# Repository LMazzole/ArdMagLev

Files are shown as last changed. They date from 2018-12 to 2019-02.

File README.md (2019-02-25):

# ArdMagLev
This Project is based on the [AirBonsai](https://www.instructables.com/id/Arduino-Air-Bonsai-Levitation/)-Project from Funelab.  

- [General Setup](#general-setup)
- [Initial Problems](#initial-problems)
- [Improvments](#improvments)
- [Result](#result)
- [Remaining Problems](#remaining-problems)
- [TODO's](#todos)

## General Setup
### IDE
[PlatformIO ](https://platformio.org/platformio-ide)

### Board
Arduino Leonardo

## Initial Problems

### Coils
One of the biggest Problems is, that the generated Field of the Coils will disturb your Hallsensor.  
Without the correct Sensorvalue you won't be able to controll the position.
[TODO: Add Calculation Tau]
### Position of the Hallsensor
The proposed setup with the Breadboard has the disadvantage, that you're not able to orient the Hallsensor correctly. Horizontal und vertical displacements have a negative influence on the precision of the Sensors and increase the disturbance from the Coils.  

As you can see in the Image below the Sensor will detect the Field from the Coils much more if they are not completly parallel.  

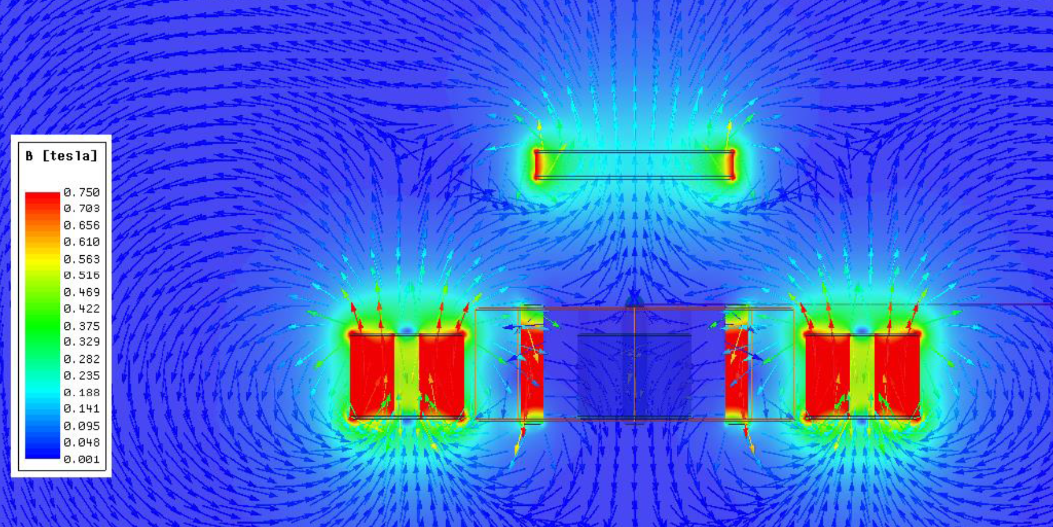
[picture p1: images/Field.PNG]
Field


## Improvements

### System-Overview

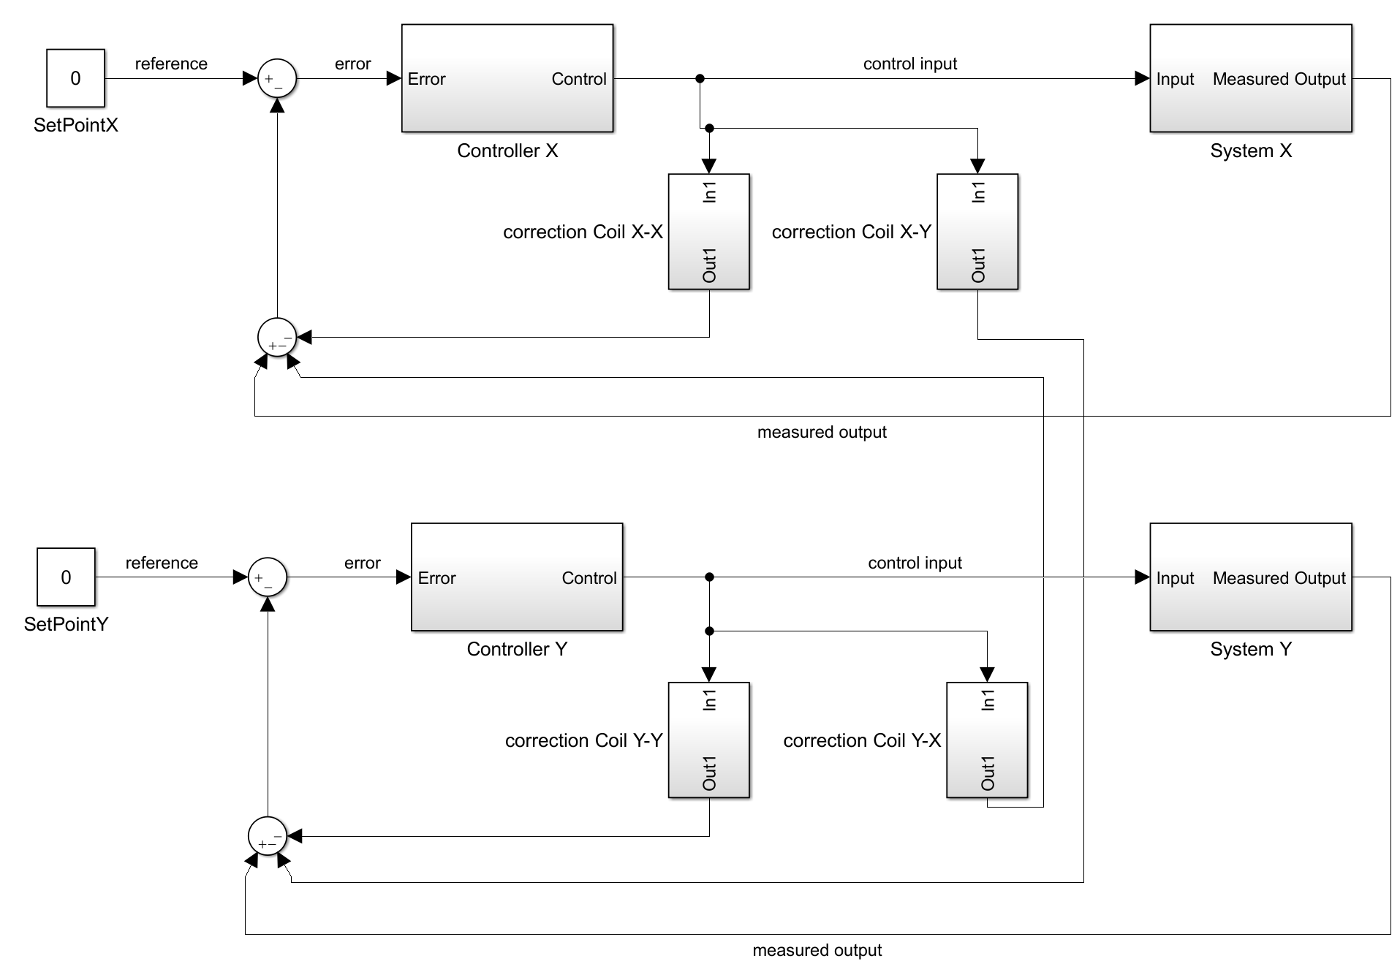
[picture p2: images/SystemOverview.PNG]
SystemOverview


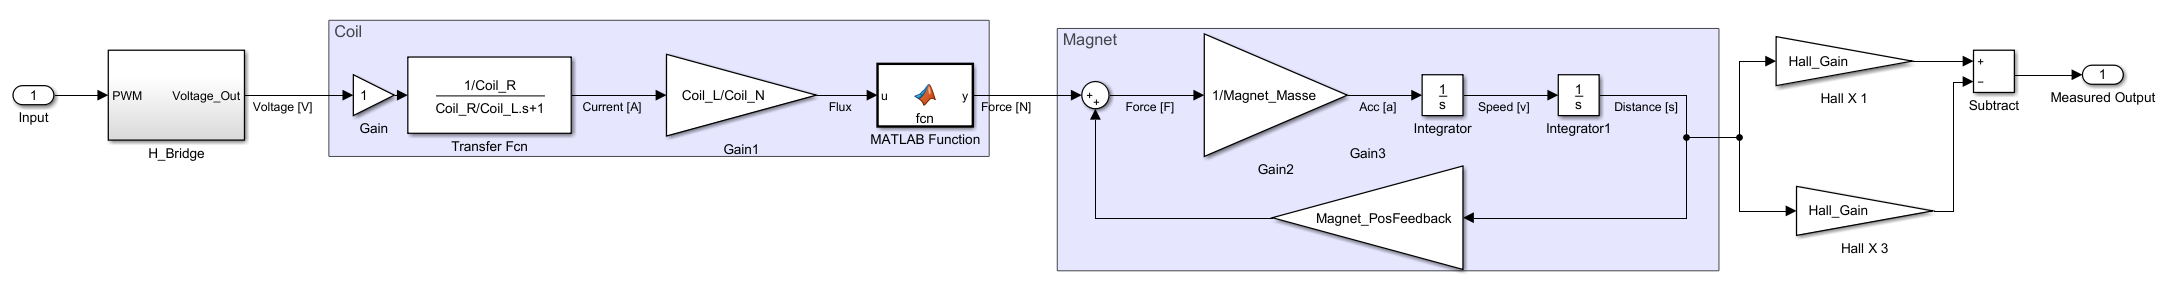
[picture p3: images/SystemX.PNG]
SystemX


### Hardware
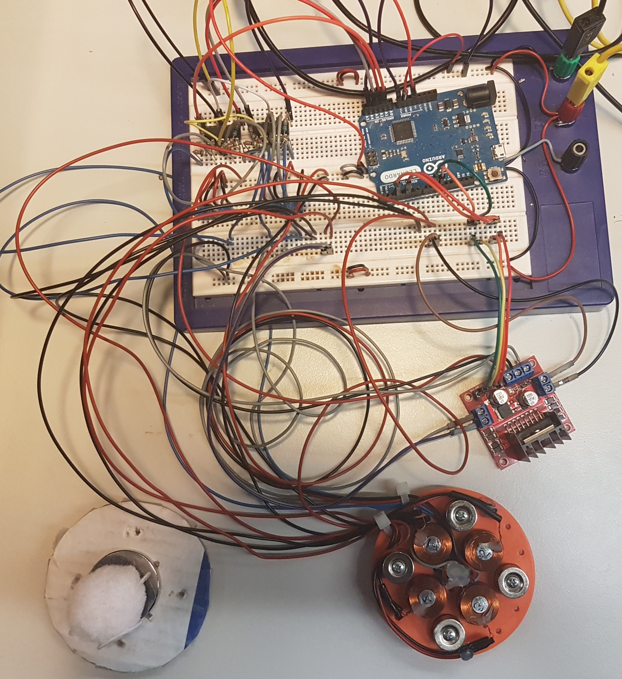
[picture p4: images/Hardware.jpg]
Hardware


### 3D-Print
To solve the Position-Problem and make a more reproducible Design a 3D-Print was created. 

[Check the Folder](./3D-Data/) for the .stl or .prt (Siemens NX 12)

### Hall-Sensors
[SS495A-S Datasheet](https://sensing.honeywell.com/honeywell-sensing-sensors-linear-hall-effect-ics-ss490-series-datasheet-005843-2-en.pdf)  
To minimize the Coil-influence, two more Hallsensores were added.  

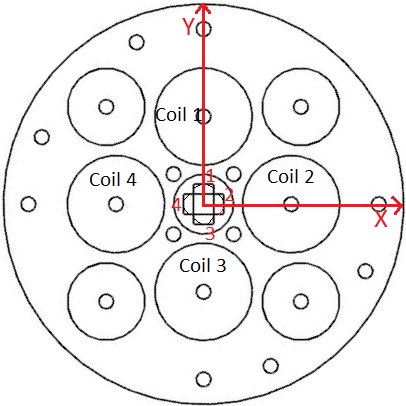
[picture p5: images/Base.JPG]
Base


### Software
#### Preprocessor Directives
To switch between the different Modes comment or uncomment the #defines at the beginning of the Sketch.

##### MYDEBUG
This Mode will display debugg-messages over the Serial-Port

##### MYTIMING
This Mode will display the time needed for one Loop  over the Serial-Port

##### TESTX
This Mode will power the Coils on the X-Axis in Steps from 0 to 255 and 0 to -255.  

At 255 your Input_X should be an negativ Value.  
At -255 your Input_X should be an positiv Value.
##### TESTY
This Mode will power the Coils on the Y-Axis in Steps from 0 to 255 and 0 to -255.  

At 255 your Input_Y should be an negativ Value.  
At -255 your Input_Y should be an positiv Value.
##### TESTXY
This Mode will move your Magnet in an rectangle.

##### CONTROLL
This Mode will activate the PID-Controller.

##### AUTOSHUTDOWN
This Mode will activate the Autoshutdown.  
If your Controll fails and the Magnet falls from its centerpoint the Controller will set the PWM to 100%. This will overheat your Coils and destroy them.  

To prevent this, the Autoshutdown will power off the Coils if the Output is too high for too long.

##### BREAKMODE

An Instructabel User recommended to use the breaking mode for the H-Bridge.  

>After playing around with the H bridge I found that its output current is way more predictable by leaving the jumpers on ENA and ENB, and applying pwm directly to the IN pins: (eg: If the output value from the pid is positive, IN1 is low, and IN2 is fed the pwm wave. If the output is negative, IN2 is low, and IN1 is fed the pwm wave). This is the "braking mode" when the bridge is used to drive dc motors, so the coil ends are short circuited between the pwm pulses instead of being at high impedance.
> -- <cite> Simo_Dax </cite> 

#### Corrct Coil-Influence
The function *corr_sensor_x* and *corr_sensor_y* will read the actual PWM-Output and calculate the error generated in the Sensors. You probably will need to update this calculation for your own setup.

## Result
Base

### Technical Details
- Max Load: [Todo: measure]
- Normal Power-consumption: ca. 0.4 A
- Max Power-consumption: ca. 2.5 A

## Remaining Problems

### Tuning/Stability
A little bit of luck is needed to find the correct parameters. If your about 0.2 off it will probably not be stable.

### Noise
Unfortunately because of the low PWM frequency the Coils are VERY noisy.  
An Higher PWM frequency would solve this Problem.

### Magnet detection
There is no Standby-Mode atm. A Function for the detection of the floating Magnet is necessary.

## TODOs
Feel free to contribute
- Improve Instructions
- Update Controller for Higher PWM and to minimize Coil-Noise
- Implement detection for the floating magnet
- Write an PID-Controller and delete the library

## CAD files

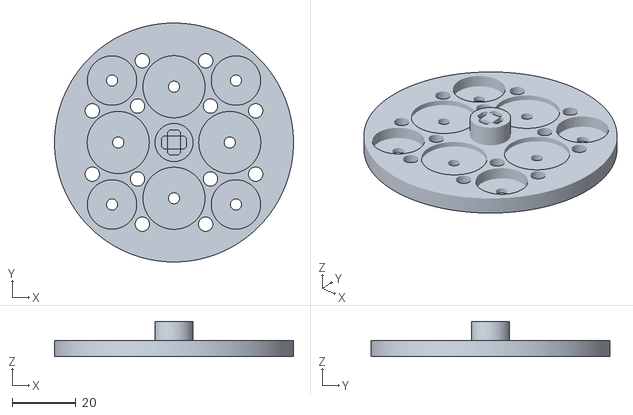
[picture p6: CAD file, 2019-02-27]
3D-Data/MagLev-Base_V3.stl
75.0 x 75.0 x 11.0

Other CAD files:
3D-Data/MagLev-Base_V3.prt

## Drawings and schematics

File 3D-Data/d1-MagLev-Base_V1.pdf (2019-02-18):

1

A

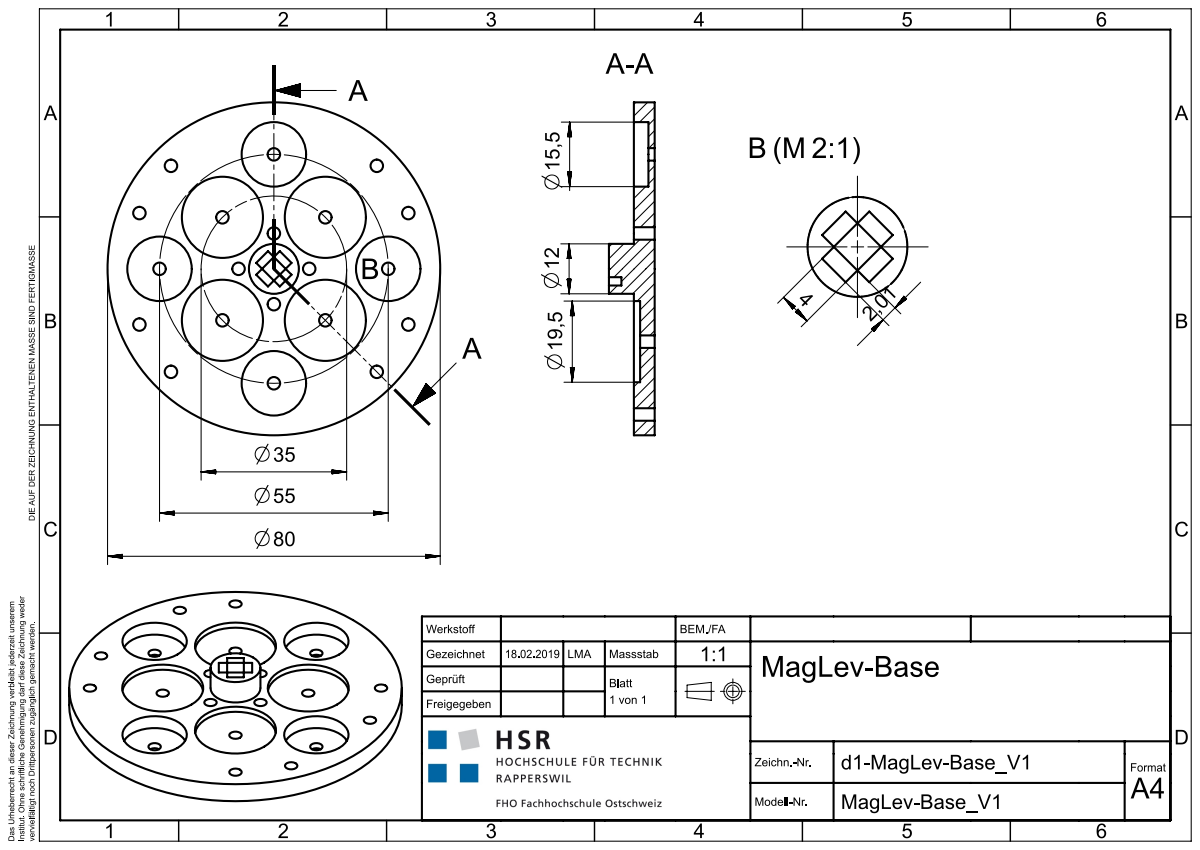
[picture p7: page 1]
Werkstoff; BEM./FA; Gezeichnet; LMA; Massstab; Geprüft; MagLev-Base Blatt; Freigegeben; 1 von 1; Zeichn.-Nr.; d1-MagLev-Base_V1; Format; Modell-Nr.; A4 MagLev-Base_V1

vervielfältigt noch Drittpersonen zugänglich gemacht werden. DIE AUF DER ZEICHNUNG ENTHALTENEN MASSE SIND FERTIGMASSE

Das Urheberrecht an dieser Zeichnung verbleibt jederzeit unserem

Institut. Ohne schriftliche Genehmigung darf diese Zeichnung weder

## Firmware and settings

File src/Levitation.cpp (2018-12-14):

#include <PID_v1.h>
#include "Arduino.h"

// #define MYDEBUG
// #define MYTIMING

#define CONTROLL
// #define TESTX
// #define TESTY
// #define TESTXY

//Define Debug-Function
#ifdef MYDEBUG
  #define DEBUG_PRINT(x)        Serial.print (x)
  #define DEBUG_PRINTDEC(x)     Serial.print (x, DEC)
  #define DEBUG_PRINTLN(x)      Serial.println (x)
#else
  #define DEBUG_PRINT(x)
  #define DEBUG_PRINTDEC(x)
  #define DEBUG_PRINTLN(x)
#endif

#ifdef MYTIMING
  #define TIMING_PRINT(x)        Serial.print (x)
  #define TIMING_PRINTDEC(x)     Serial.print (x, DEC)
  #define TIMING_PRINTLN(x)      Serial.println (x)
#else
  #define TIMING_PRINT(x)
  #define TIMING_PRINTDEC(x)
  #define TIMING_PRINTLN(x)
#endif

const byte ENA = 10;
const byte IN1 = 9; //9Enable for Out 1 X_Plus
const byte IN2 = 8; //8Enable for Out 2 X_Minus
const byte IN3 = 7; //Enable for Out 3 Y_Plus
const byte IN4 = 6; //Enable for Out 4 Y_Minus
const byte ENB = 5;
const byte HALLX = A1;
const byte HALLY = A0;

const byte anzahlMittelWerte = 3;
int werteHallX[anzahlMittelWerte], zaehlerMittelWerteX=0;
int werteHallY[anzahlMittelWerte], zaehlerMittelWerteY=0;
int mittelWertX(int neuerWert);
int mittelWertY(int neuerWert);

unsigned long time_loop_start;
unsigned long time_loop_stop;

double Setpoint_X, X_plus;
static double Input_X, Output_X;
double p_X = 2,i_X = 0,d_X = 0.005;
// double p_X = 1.0,i_X = 0.0,d_X = 0.01;

double Setpoint_Y, Y_plus;
static double Input_Y, Output_Y;
double p_Y = 2,i_Y = 0,d_Y = 0.005;
// double p_Y = 1.0,i_Y = 0.0,d_Y = 0.01;
PID PID_X(&Input_X, &Output_X, &Setpoint_X, p_X,i_X,d_X, DIRECT);
PID PID_Y(&Input_Y, &Output_Y, &Setpoint_Y, p_Y,i_Y,d_Y, DIRECT);

void turn_X(int a);
void turn_Y(int a);
void read_sensor();
void turn_off();
int corr_sensor_y(double pwm_y);
int corr_sensor_x(double pwm_x);
double pid_ctrl_X(double error);
double pid_ctrl_Y(double error);


void setup(){
  Serial.begin(4800);
  pinMode(IN1,OUTPUT);
  pinMode(IN2,OUTPUT);
  pinMode(IN3,OUTPUT);
  pinMode(IN4,OUTPUT);
  pinMode(ENA,OUTPUT);
  pinMode(ENB,OUTPUT);

  digitalWrite(IN1,0);
  digitalWrite(IN2,0);
  digitalWrite(IN3,0);
  digitalWrite(IN4,0);
  analogWrite(ENA,0);
  analogWrite(ENB,0);


  Setpoint_X = 560;//560;
  PID_X.SetTunings(p_X,i_X,d_X);
  PID_X.SetOutputLimits(-255,255);
  PID_X.SetSampleTime(10);//10
  PID_X.SetMode(AUTOMATIC);
  PID_X.SetControllerDirection(REVERSE);

  Setpoint_Y = 560;//560;
  PID_Y.SetTunings(p_Y,i_Y,d_Y);
  PID_Y.SetOutputLimits(-255,255);
  PID_Y.SetSampleTime(10);//10
  PID_Y.SetMode(AUTOMATIC);
  PID_Y.SetControllerDirection(REVERSE);//DIRECT or REVERSE

turn_off();
}

void loop(){
  // DEBUG_PRINTLN("");
  TIMING_PRINT("Time passed [ms]:"); TIMING_PRINTLN((double)(time_loop_stop-time_loop_start));
  time_loop_start=millis();
  Input_X = analogRead(HALLX)-corr_sensor_y(Output_X);
  Input_Y = analogRead(HALLY)-corr_sensor_y(Output_Y);
  // Input_X = mittelWertX(Input_X);
  // Input_Y = mittelWertY(Input_Y);
    // read_sensor();
  #ifdef CONTROLL //Regeln
  read_sensor();
    //Compute correction Value
    //===PID====
    // time_loop_stop=millis();
    // TIMING_PRINT("Time passed [ms]:"); TIMING_PRINTLN((double)(time_loop_stop-time_loop_start));
    PID_X.Compute();
    PID_Y.Compute();
    // time_loop_start=millis();
    turn_X(Output_X);
    turn_Y(Output_Y);
  #endif

  #ifdef TESTX
  DEBUG_PRINTLN("");
  DEBUG_PRINTLN("===TESTX====");
    int valx = 0;
    int delaytestx=750;
    while (valx<255) {
      turn_X(valx);
      read_sensor();
      valx+=10;
      delay(delaytestx);
    }
    turn_X(0);
    DEBUG_PRINTLN("=======");
    delay(1000);
    valx = 0;
    while (valx<255) {
      turn_X(-valx);
      read_sensor();
      valx+=10;
      delay(delaytestx);
    }
    turn_X(0);
    // delay(10000);
  #endif

  #ifdef TESTY
  DEBUG_PRINTLN("");
  DEBUG_PRINTLN("===TESTY====");
    int valy = 0;
    int delaytesty=750;
    while (valy<255) {
      turn_Y(valy);
      read_sensor();
      valy+=10;
      delay(delaytesty);
    }
    turn_Y(0);
    DEBUG_PRINTLN("=======");
    delay(1000);
    valy = 0;
    while (valy<255) {
      turn_Y(-valy);
      read_sensor();
      valy+=10;
      delay(delaytesty);
    }
    turn_Y(0);
    delay(5000);
  #endif

  #ifdef TESTXY
    DEBUG_PRINTLN("=====TESTXY=====");
    int delayTest=2000;
    turn_X(255); //Oben
    delay(delayTest);
    read_sensor();
    turn_off();
    turn_Y(255); //Rechts
    delay(delayTest);
    read_sensor();
    turn_off();
    turn_X(-255); //Unten
    delay(delayTest);
    read_sensor();
    turn_off();
    turn_Y(-255); //Links
    delay(delayTest);
    read_sensor();
    turn_off();
    read_sensor();
    delay(5000);
  #endif

  time_loop_stop=millis();
}

void turn_X(int a){
  Output_X=a;
  DEBUG_PRINT("turn_X: ");DEBUG_PRINT("\t"); DEBUG_PRINT(a);DEBUG_PRINT("\t");
  if(a>=0)  {
    DEBUG_PRINT(" Oben");
    digitalWrite(IN2,0);
    digitalWrite(IN1,1);
    analogWrite(ENA,a);
  }
  else  {
    DEBUG_PRINT(" Unten");
    a=-a;
    digitalWrite(IN1,0);
    digitalWrite(IN2,1);
    analogWrite(ENA,a);
  }
  // DEBUG_PRINT("\t");
  // DEBUG_PRINTLN("");
}

void turn_Y(int a){
  Output_Y=a;
DEBUG_PRINT("turn_Y: ");DEBUG_PRINT("\t"); DEBUG_PRINT(a);DEBUG_PRINT("\t");
  if(a>=0)  {
    DEBUG_PRINT(" Rechts");
    digitalWrite(IN4,0);
    digitalWrite(IN3,1);
    analogWrite(ENB,a);
  }
  else{
    DEBUG_PRINT(" Links");
    a=-a;
    digitalWrite(IN3,0);
    digitalWrite(IN4,1);
    analogWrite(ENB,a);
  }
  // DEBUG_PRINT("\t");
  // DEBUG_PRINTLN("");
}

void turn_off(){
  digitalWrite(IN1,0);
  digitalWrite(IN2,0);
  digitalWrite(IN3,0);
  digitalWrite(IN4,0);
  Output_X=0;
  Output_Y=0;
  analogWrite(ENA,Output_X);
  analogWrite(ENB,Output_Y);
  delay(100);
}

void read_sensor(){
  Input_X = analogRead(A1);
  Input_Y = analogRead(A0);
  DEBUG_PRINT("\t");
  // DEBUG_PRINT("\t");DEBUG_PRINT("\t");DEBUG_PRINT("\t");
  DEBUG_PRINT("Input_X: ");DEBUG_PRINT("\t");
  DEBUG_PRINT(Input_X);DEBUG_PRINT("\t");
  DEBUG_PRINT("corr: ");DEBUG_PRINT("\t");
  DEBUG_PRINT(Input_X-corr_sensor_x(Output_X));
  // DEBUG_PRINTLN("");//DEBUG_PRINT("\t");
  DEBUG_PRINT("\t");
  DEBUG_PRINT("Input_Y: ");DEBUG_PRINT("\t");
  DEBUG_PRINT(Input_Y);DEBUG_PRINT("\t");
  DEBUG_PRINT("corr: ");DEBUG_PRINT("\t");
  DEBUG_PRINT(Input_Y-corr_sensor_y(Output_Y));DEBUG_PRINTLN("");
}

int mittelWertX(int neuerWert) {
// neuen int Wert eingeben und den Mittelwert als fSloat zurück geben
//
// Matthias Busse 9.2.2016 Version 1.0
float mittel, summe=0;
  werteHallX[zaehlerMittelWerteX] = neuerWert;
  for(int k=0; k < anzahlMittelWerte; k++) summe += werteHallX[k];
  mittel=(float) summe / anzahlMittelWerte;
  zaehlerMittelWerteX++;
  if(zaehlerMittelWerteX >= anzahlMittelWerte) zaehlerMittelWerteX=0;
  return mittel;
}

int mittelWertY(int neuerWert) {
// neuen int Wert eingeben und den Mittelwert als float zurück geben
//
// Matthias Busse 9.2.2016 Version 1.0
float mittel, summe=0;
  werteHallY[zaehlerMittelWerteY] = neuerWert;
  for(int k=0; k < anzahlMittelWerte; k++) summe += werteHallY[k];
  mittel=(float) summe / anzahlMittelWerte;
  zaehlerMittelWerteY++;
  if(zaehlerMittelWerteY >= anzahlMittelWerte) zaehlerMittelWerteY=0;
  return mittel;
}

int corr_sensor_y(double x){
  // return 0;
  if (x==0){
    return 0;
  }
  else{
    double corrval;
    // corrval= 0.01*x*x*x - 0.88*x*x + 22*x;// -176;
    corrval=1.13/100000*x*x*x+9.70/1000000*x*x-0.08*x+0.113;
    // corrval= (0.1132*x - 0.0828)*x*x;
    // corrval=(0.000009*x*x-0.0001*x-0.08)*x; //corrval=(0.000009*x*x-0.0001*x-0.08)*x;
    // DEBUG_PRINTLN(corrval);
    // DEBUG_PRINTLN((int)corrval);
    return (int)corrval;
  }
}

int corr_sensor_x(double x){
  if (x==0){
    return 0;
  }
  else{
    double corrval;
    corrval=1.13/100000*x*x*x+9.70/1000000*x*x-0.08*x+0.113;
    // corrval=(0.000008*x*x-0.0001*x+0.006)*x;
    // DEBUG_PRINTLN(corrval);
    // DEBUG_PRINTLN((int)corrval);
    return (int)corrval;
  }
}
// double pid_ctrl_X(double error) { //PID without library
//   static double X_esum;
//   static double X_ealt;
//   double y;
//
//   esum = X_esum + error;
//   y = p_X * error + i_X * x_Ta * esum + d_X * (error – X_ealt)/X_Ta;
//   ealt = error;
//
//   return y;
// }

// double pid_ctrl_Y(double e) { //PID without library
//   static double esum;
//   static double ealt;
//   double y;
//
//   esum = esum + e;
//   y = Kp * e + Ki * Ta * esum + Kd * (e – ealt)/Ta;
//   ealt = e;
//
//   return y;
// }

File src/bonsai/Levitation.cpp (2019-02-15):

/*%
-----------------------------------------------------------------------
% Dateiname: Levitation.cpp

% Funktion: Regelung eines fliegenden Magneten
%           Grundlage: https://www.instructables.com/id/Arduino-Air-Bonsai-Levitation/
% Autor: Luca Mazzoleni  lmazzole@hsr.ch
%
% Erstellungsdatum: 08.12.2018
% Letzte Änderung:  19.12.2018
%-----------------------------------------------------------------------
*/


#include <PID_v1.h>
#include "Arduino.h"

// #define MYDEBUG
// #define MYTIMING

// #define TESTX
// #define TESTY
// #define TESTXY

#define CONTROLL
#define AUTOSHUTDOWN
#define BREAKERMODE


//Define Debug-Function
#ifdef MYDEBUG
  #define DEBUG_PRINT(x)        Serial.print (x)
  #define DEBUG_PRINTDEC(x)     Serial.print (x, DEC)
  #define DEBUG_PRINTLN(x)      Serial.println (x)
#else
  #define DEBUG_PRINT(x)
  #define DEBUG_PRINTDEC(x)
  #define DEBUG_PRINTLN(x)
#endif

#ifdef MYTIMING
  #define TIMING_PRINT(x)        Serial.print (x)
  #define TIMING_PRINTDEC(x)     Serial.print (x, DEC)
  #define TIMING_PRINTLN(x)      Serial.println (x)
  unsigned long time_loop_start;
  unsigned long time_loop_stop;
#else
  #define TIMING_PRINT(x)
  #define TIMING_PRINTDEC(x)
  #define TIMING_PRINTLN(x)
#endif

// PINMAPPING
#ifdef BUILD_FOR_NANO
  const byte ENA = 10;
  const byte IN1 = 9; //9Enable for Out 1 X_Plus
  const byte IN2 = 8; //8Enable for Out 2 X_Minus
  const byte IN3 = 7; //Enable for Out 3 Y_Plus
  const byte IN4 = 6; //Enable for Out 4 Y_Minus
  const byte ENB = 5;
  const byte HALLX = A1;
  const byte HALLY = A0;
#endif

#ifdef BUILD_FOR_LEONARDO
  const byte ENA = 12;
  const byte IN1 = 3; //Enable for Out 1 X_Plus
  const byte IN2 = 5; //Enable for Out 2 X_Minus
  const byte IN3 = 10; //Enable for Out 3 Y_Plus
  const byte IN4 = 11; //Enable for Out 4 Y_Minus
  const byte ENB = 12;

  const byte HALL1 = A1;
  const byte HALL2 = A2;
  const byte HALL3 = A3;
  const byte HALL4 = A4;
#endif
//

#ifdef AUTOSHUTDOWN
  const int shutdown_treshhold = 200;
  int shutdown_val=0;
#endif

// #ifdef CONTROLL
double Setpoint_X, X_plus;
static double Input_X, Output_X;
double p_X = 0.8,i_X = 0.00,d_X = 0.008;
// double p_X = 1.0,i_X = 0.0,d_X = 0.01;

double Setpoint_Y, Y_plus;
static double Input_Y, Output_Y;
double p_Y = 0.8,i_Y = 0.00,d_Y = 0.008;
// double p_Y = 1.0,i_Y = 0.0,d_Y = 0.01;
PID PID_X(&Input_X, &Output_X, &Setpoint_X, p_X,i_X,d_X, DIRECT);
PID PID_Y(&Input_Y, &Output_Y, &Setpoint_Y, p_Y,i_Y,d_Y, DIRECT);
// #endif

//Functionprototyp
void turn_X(int a);
void turn_Y(int a);
void read_sensor();
void turn_off();
int corr_sensor_y(double pwm_y);
int corr_sensor_x(double pwm_x);
double pid_ctrl_X(double error);
double pid_ctrl_Y(double error);

void setup(){
  #ifdef MYDEBUG
    Serial.begin(4*4800);
  #endif

  pinMode(IN1,OUTPUT);
  pinMode(IN2,OUTPUT);
  pinMode(IN3,OUTPUT);
  pinMode(IN4,OUTPUT);
  pinMode(ENA,OUTPUT);
  pinMode(ENB,OUTPUT);

  Setpoint_X = 0;//560;
  PID_X.SetTunings(p_X,i_X,d_X);
  PID_X.SetOutputLimits(-255,255);
  PID_X.SetSampleTime(5); // Sampletime in milliseconds
  PID_X.SetMode(AUTOMATIC);
  PID_X.SetControllerDirection(DIRECT);

  Setpoint_Y = 10;//560;
  PID_Y.SetTunings(p_Y,i_Y,d_Y);
  PID_Y.SetOutputLimits(-255,255);
  PID_Y.SetSampleTime(5); // Sampletime in milliseconds
  PID_Y.SetMode(AUTOMATIC);
  PID_Y.SetControllerDirection(DIRECT);//DIRECT or REVERSE

  turn_off();
}

void loop(){
  // DEBUG_PRINTLN("");
  #ifdef MYTIMING
    TIMING_PRINT("Time passed [ms]:"); TIMING_PRINTLN((double)(time_loop_stop-time_loop_start));
    time_loop_start=millis();
  #endif

  read_sensor();
  Input_X-=0.7*corr_sensor_x(Output_X);
  Input_Y-=0.7*corr_sensor_y(Output_Y);
  // Input_X=mittelWertX(Input_X);
  // Input_Y=mittelWertX(Input_Y);

  #ifdef CONTROLL //Regeln
    PID_X.Compute();
    PID_Y.Compute();
    #ifdef AUTOSHUTDOWN
      if(abs(Output_X)>254 || abs(Output_X)>254){
          shutdown_val+=1;
          DEBUG_PRINTLN("");
          DEBUG_PRINT("shutdown_val");DEBUG_PRINTLN(shutdown_val);
      }
      else{
        shutdown_val=0;
      }
      if(shutdown_val>shutdown_treshhold){
        DEBUG_PRINTLN("");
        DEBUG_PRINTLN("TURN OFF");
        turn_off();
        delay(3000);//cooldown
        while(abs(Input_X) >10 && abs(Input_Y) >10 ){
          DEBUG_PRINTLN("WAIT FOR INITPOS");
          read_sensor();
          delay(100);
        }
        shutdown_val=0;
      }
    #endif
    turn_X(Output_X);
    turn_Y(Output_Y);
  #endif

  #ifdef TESTX
    DEBUG_PRINTLN("");
    DEBUG_PRINTLN("===TESTX====");
    int valx = 0;
    int delaytestx=750/2;
    while (valx<255) {
      turn_X(valx);
      delay(delaytestx);
      read_sensor();
      delay(delaytestx);
      valx+=10;
    }
    turn_X(0);
    DEBUG_PRINTLN("=======");
    delay(1000);
    valx = 0;
    while (valx<255) {
      turn_X(-valx);
      delay(delaytestx);
      read_sensor();
      delay(delaytestx);
      valx+=10;
    }
    turn_X(0);
  #endif

  #ifdef TESTY
    DEBUG_PRINTLN("");
    DEBUG_PRINTLN("===TESTY====");
    int valy = 0;
    int delaytesty=750/2;
    while (valy<255) {
      turn_Y(valy);
      delay(delaytesty);
      read_sensor();
      delay(delaytesty);
      valy+=10;
    }
    turn_Y(0);
    DEBUG_PRINTLN("=======");
    delay(1000);
    valy = 0;
    while (valy<255) {
      turn_Y(-valy);
      delay(delaytesty);
      read_sensor();
      delay(delaytesty);
      valy+=10;
    }
    turn_Y(0);
    delay(5000);
  #endif

  #ifdef TESTXY
    DEBUG_PRINTLN("=====TESTXY=====");
    int delayTest=2000;
    turn_X(255); //Oben
    delay(delayTest);
    read_sensor();
    turn_off();
    turn_Y(255); //Rechts
    delay(delayTest);
    read_sensor();
    turn_off();
    turn_X(-255); //Unten
    delay(delayTest);
    read_sensor();
    turn_off();
    turn_Y(-255); //Links
    delay(delayTest);
    read_sensor();
    turn_off();
    read_sensor();
    delay(5000);
  #endif

  #ifdef MYTIMING
    time_loop_stop=millis();
  #endif
}

//=============================================================================
void turn_X(int a){
  Output_X=a;
  DEBUG_PRINT("turn_X: ");DEBUG_PRINT("\t"); DEBUG_PRINT(a);DEBUG_PRINT("\t");
  if(a>=0)  {
    DEBUG_PRINT("Rechts");
    digitalWrite(IN2,0);
    #ifdef BREAKERMODE
      analogWrite(IN1,a);
    #else
      digitalWrite(IN1,1);
      analogWrite(ENA,a);
    #endif
  }
  else  {
    DEBUG_PRINT("Links");
    a=-a;
    digitalWrite(IN1,0);
    #ifdef BREAKERMODE
      analogWrite(IN2,a);
    #else
      digitalWrite(IN2,1);
      analogWrite(ENA,a);
    #endif
  }
  DEBUG_PRINT("\t");
  // DEBUG_PRINTLN("");
}
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

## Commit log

2018-12-14 corr sensor-data
2019-02-14 added Sensor-Corr and switched to single H-Bridge
2019-02-18 draft README
    [MagLev-Base_V1.prt, MagLev-Base_V1.stl]
2019-02-27 updated 3D-Parts
    [MagLev-Base_V1.prt, MagLev-Base_V1.stl, MagLev-Base_V3.prt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]
